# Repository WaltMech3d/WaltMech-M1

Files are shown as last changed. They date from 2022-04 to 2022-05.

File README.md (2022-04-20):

# `M1`

`The WaltMech M1 is the successor project of the MouseRig
- print volume: 150x150x150
- Framesize:    xyz 296x344x440 
- [Fusion 360 viewer](https://a360.co/3rA96aa)
- [Eva Parts](https://main.eva-3d.page/)



`summary of the changes and improvements:` 
- custom aluminum sheets have been removed
- the drive runs on ball bearings and 6mm belts
- the XY-drive was placed on top of the profiles
- the filter is integrated in the housing
- Reduced size of V2 compared to MouseRig 
- smaller motors were used for the Z axis
- blind joints instead of corner plates
- much less screws and hammer nuts
- The number of profiles has been reduced
- Easier to build and much more cost-efficient than the previous model



-----------------------------------------------------------------------
Special thanks to Liam Venter for letting me use his Ventermech Stars

[fastbikegear.co.nz](https://www.fastbikegear.co.nz/index.php?main_page=product_info&cPath=3717&products_id=12371)

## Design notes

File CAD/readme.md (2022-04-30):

30.04.2022:
Cad data have been updated. Radius on the filter box was adjusted + clearance for the cable of the fan was added.

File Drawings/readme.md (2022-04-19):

Drawings for:

- Side Panel with cutout
- Bottom Panel
- Back Panel Top
- Electro Panel
- Aluminium Plate for heated bed

The rest of the panels are rectangular with no cutouts. the dimensions can be taken from the CAD model or the BOM

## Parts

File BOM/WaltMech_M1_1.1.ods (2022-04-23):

1. ASM Frame + Enclosure
Pos. | Quantity | Designation | Dimension | Material / DIN | Supplier | Notes
1.01 | 4 | ALTRAX aluminum profile | 20x20x440 | Al | Hobby-store.pl (https://hobby-store.pl/profile-aluminiowe/typ-t-slot-20) | Special care should be applied when sourcing profiles. V-slot should be avoided, and bigger inside cores are encouraged to provide the strongest blind-joint connection. When using sliding t-nuts the groove should be of at least 6,5mm.
1.02 | 6 | ALTRAX aluminum profile | 20x20x304 | Al
1.03 | 7 | ALTRAX aluminum profile | 20x20x256 | Al
1.04 | 2 | ALTRAX aluminum profile | 20x20x225 | Al
1.05 | 1 | ALTRAX aluminum profile | 20x20x205 | Al
1.06 | 1 | ALTRAX aluminum profile | 20x20x267 | Al
1.07 | 64 | T Nut | m4 | TypB | Aliexpress (https://de.aliexpress.com/item/33024399415.html?pdp_ext_f=%7b%22sku_id%22%3A%2267203262268%22%7d)
1.08 | 102 | T Nut | m3 | Typ B | Aliexpress (https://de.aliexpress.com/item/33024399415.html?pdp_ext_f=%7b%22sku_id%22%3A%2267203262268%22%7d)
1.09 | 9 | Nut | m4 | DIN 934
1.10 | 28 | Nut | m3 | DIN 934
1.11 | 4 | Ny-lock Nut | m5 | DIN 982
1.12 | 16 | Threaded Insert m3 | m3x5x4 |  | Aliexpress (https://de.aliexpress.com/item/4000232858343.html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)
1.13 | 24 | Washer | m5 | DIN 125
1.14 | 4 | m3x5 cylindrical | m3 | DIN 912
1.15 | 4 | m3x6 cylindrical | m3 | DIN 912
1.16 | 4 | m3x6 Countersunk | m3 | DIN 7991
1.17 | 125 | m3x8 cylindrical | m3 | DIN 912
1.18 | 8 | m3x10 Countersunk | m3 | DIN 7991
1.19 | 6 | m3x14 Countersunk | m3 | DIN 7991
1.20 | 35 | m3x14 cylindrical | m3 | DIN 912
1.21 | 44 | m4x10 Button-Head Screw | m4 | ISO 7380-1
1.22 | 12 | m4x12 Button-Head Screw | m4 | ISO 7380-1
1.23 | 13 | m4x20 Button-Head Screw | m4 | ISO 7380-1
1.24 | 4 | m4x35 Button-Head Screw | m4 | ISO 7380-1
1.25 | 37 | m5x16 Button-Head Screw | m5 | ISO 7380-1
1.26 | 3 | m5x16 Countersunk | m5 | DIN 7991
1.27 | 2 | m5x20 cylindrical | m5 | DIN 912
1.28 | 4 | m5x35 Button-Head Screw | m5 | ISO 7380-1
1.29 | 4 | m5x45 Button-Head Screw | m5 | ISO 7380-1
1.30 | 8 | ST FAN-SCREW | 5x10 |  |  | supplied with fans
1.31 | 1 | Front Panel | 440x296x3 | acrylic glass
1.32 | 2 | Side Panel | 414x318x3 | ABS
1.33 | 1 | Top Panel | 318x270x3 | ABS
1.34 | 1 | Lower back Panel | 280x270x3 | ABS
1.35 | 1 | Top back Panel | 270x147x3 | ABS
1.36 | 1 | Bottom Panel | 256x234x3 | ABS
1.37 | 2 | Skirt Panel 1 | 304x30x3 | ABS
1.38 | 2 | Skirt Panel 2 | 256x30x3 | ABS
1.39 | 1 | Elektro Panel | 440x296x3 | ABS
2. Linear guide , Bed , etc.
Pos. | Quantity | Designation | Dimension | Material / DIN | Supplier | Notes
2.01 | 1 | MGN12C | 200mm |  | Aliexpress (https://de.aliexpress.com/item/32829826159.html?scm_id=1007.22922.122102.0&scm-url=1007.22922.122102.0)
2.02 | 5 | MGN9H | 200mm |  | Aliexpress (https://de.aliexpress.com/item/32773296501.html?spm=a2g0o.cart.0.0.697a3c00QbYMLn&mp=1)
2.03 | 3 | Spider Coupler | Ø20x25 /5-8 |  | Aliexpress (https://fr.aliexpress.com/item/32576954099.html?pdp_ext_f=%7b%22sku_id%22%3A%2264792222206%22%7d)
2.04 | 3 | Lead Screw | TR8x4x210 |  | Aliexpress (https://de.aliexpress.com/item/1005003425426272.html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)
2.05 | 2 | Nema17 x 48 | 42x42x48 |  | Stepperonline (https://www.omc-stepperonline.com/de/nema-17-42mm-schrittmotor/nema-17-bipolar-59ncm-84oz-in-2a-42x48mm-4draehte-w-1m-kabel-verbinder-17hs19-2004s1)
2.06 | 3 | Nema17 x 40 | 42x42x40 |  | Stepperonline (https://www.omc-stepperonline.com/de/nema-17-42mm-schrittmotor/nema-17-bipolar-45ncm-64oz-in-2a-42x42x40mm-4-draehte-w-1m-kabel-verbinder-17hs16-2004s1)
2.07 | 6 | Thrust Bearing F8-16M |  | 8x16x5mm | Aliexpress (https://de.aliexpress.com/item/32912814515.html?spm=a2g0o.cart.0.0.adcf3c000MXIuY&mp=1)
2.08 | 2 | End-stops |  |  | Aliexpress (https://de.aliexpress.com/item/32817694814.html?pdp_ext_f=%7b%22sku_id%22%3A%2264691411626%22%7d)
2.09 | 2 | Timing Pulley GT2 |  | 20T | Aliexpress (https://de.aliexpress.com/item/32788162034.html)
2.10 | 1 | PTFE Tube | 2x4 |  | Aliexpress (https://de.aliexpress.com/item/1005001408141263.html)
2.11 | 1 | GT2 Belt | 6mm x3m |  | Aliexpress (https://de.aliexpress.com/item/32853559638.html)
2.12 | 24 | Ball-bearing F695-2RS | 5 x 13 x 4 | FUSHIBEARING | Amazon, Aliexpress
2.13 | 4 | Neodymium magnet | Ø6x4 |  | Aliexpress (https://fr.aliexpress.com/item/4001165760765.html)
2.14 | 3 | Neodymium magnet 2 Holes | 20x10x4 |  | Aliexpress, RatRig
2.15 | 1 | Drag Chain 1m | 10x11 |  | aliexpress (https://www.aliexpress.com/item/33000014666.html)
2.16 | 4 | Rubber Feet | 20x15x8 |  | aliexpress (https://www.aliexpress.com/item/32980790365.html?scm_id=1007.40000.267768.0&scm-url=1007.40000.267768.0)
2.17 | 1 | Silicon heat pad | 120x120 |  | Keenovo (https://keenovo.store/collections/standard-keenovo-silicone-heaters/products/keenovo-square-silicone-heater-3d-printer-build-plate-heatbed-heating-pad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)
2.18 | 1 | PEI | 150x150 |  | Aliexpress (https://de.aliexpress.com/item/1005003636696916.html)
2.19 | 3 | Spacer | m5x6 |  | Aliexpress (https://de.aliexpress.com/item/33021606483.html?spm=a2g0o.cart.0.0.4d153c00YnOYJ2&mp=1)
2.20 | 3 | Threaded round ball | Ø12-m5 |  | Aliexpress (https://de.aliexpress.com/item/33014236308.html)
2.21 | 1 | Aluminum Plate | 165x165x6 |  | Clever3d | Easy to self source, but Clever3d offers an attractive price point for a milled cast aluminum plate for european based builders.
2.22 | 6 | Stainless dowel | Ø3x28mm |  | Amazon (https://www.amazon.de/gp/product/B00OK6GJNM/ref=ppx_yo_dt_b_asin_image_o04_s00?ie=UTF8&psc=1)
3. Print head example
Pos. | Quantity | Designation | Dimension | Material / DIN | Supplier | Notes
3.01 | 1 | Phaetus Dragon Standard Flow
3.02 | 1 | LDO Orbiter 2
3.03 | 1 | thermistor
3.04 | 1 | cartridge heater
3.05 | 1 | Blower fan | 50x15
3.06 | 1 | Axial fan | 40x40x15
3.07 | 1 | Sensor LJ12A3-4-Z/BX | m12 |  | Amazon (https://www.amazon.de/gp/product/B07XGFTV2F/ref=ppx_yo_dt_b_asin_image_o06_s00?ie=UTF8&psc=1)
4. Electronics
Pos. | Quantity | Designation | Dimension | Material / DIN | Supplier | Notes
4.01 | 1 | BTT Octopus |  |  | Amazon (https://www.amazon.de/BIGTREETECH-Mainboard-Controlle-Unterstützt-Unterstützung/dp/B098QHVBXC)
4.02 | 1 | Mean Well UHP-350-24 |  |  | Conrad (https://www.conrad.de/de/p/mean-well-uhp-350-24-ac-dc-einbaunetzteil-14-6-a-350-4-w-25-2-v-dc-ausgangsspannung-regelbar-1838048.html) | for 24v heat-bed
4.03 | 1 | Mean Well UHP-200-24 |  |  | Conrad (https://www.conrad.de/de/p/mean-well-uhp-200-24-ac-dc-einbaunetzteil-8-4-a-25-2-v-dc-ausgangsspannung-regelbar-1838286.html) | for 230v heat-bed ->recommended
4.04 | 1 | Raspberry pi Zero 2 W |  |  | BerryBase (https://www.berrybase.de/raspberry-pi/raspberry-pi-computer/boards/raspberry-pi-zero-2-w)
4.05 | 1 | SSR-25DA Fotek |  |  | Hobby-store.pl (https://hobby-store.pl/en/relays/ssr-25da-fotek-solid-state-relay-25a.html)
4.06 | 2 | be Quiet! Fan | 80mm |  | Amazon (https://www.amazon.de/quiet-BL044-Pure-Wings-Gehäuselüfter/dp/B00IOIJ4AC?__mk_de_DE=ÅMÅŽÕÑ)
4.07 | 1 | OBO Bettermann A8 | 75x75 |  | Amazon
4.08 | 6 | TMC 2209 Stepper |  |  | Aliexpress (https://de.aliexpress.com/item/33029587820.html)
4.09 | 1 | COB LED | 24v 5mm x 1m |  | Aliexpress (https://de.aliexpress.com/item/1005002701379459.html)
4.10 | 1 | Power switch |  |  | Amazon (https://www.amazon.de/gp/product/B01H5MK3OI/ref=ppx_yo_dt_b_asin_image_o05_s00?ie=UTF8&psc=1)

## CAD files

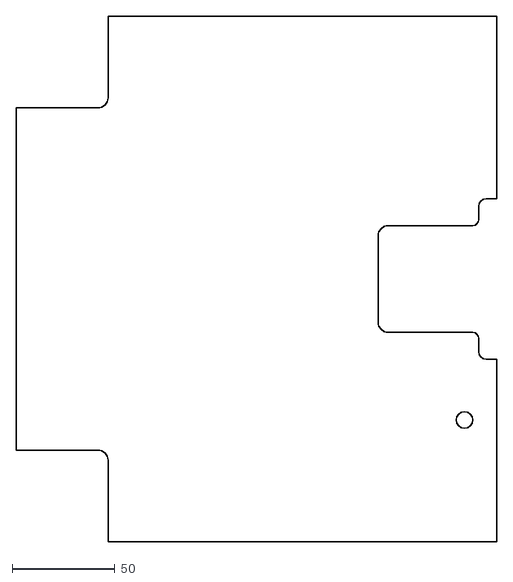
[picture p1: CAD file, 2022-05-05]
Drawings/Bottom_Panel.dxf
233.5 x 255.5

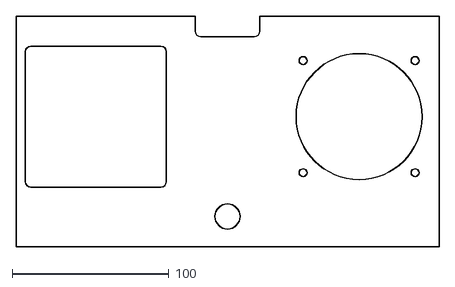
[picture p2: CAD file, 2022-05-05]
Drawings/Top_Back_Panel.dxf
270.0 x 147.0

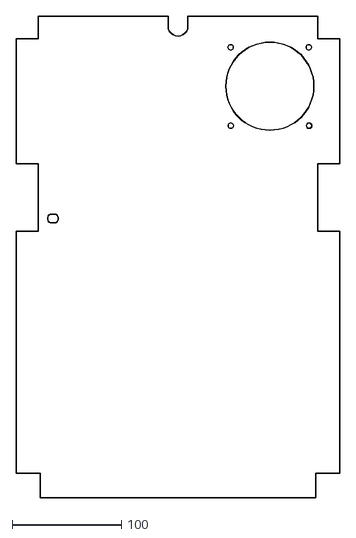
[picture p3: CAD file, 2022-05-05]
Drawings/Electronics_Panel.dxf
296.0 x 439.6

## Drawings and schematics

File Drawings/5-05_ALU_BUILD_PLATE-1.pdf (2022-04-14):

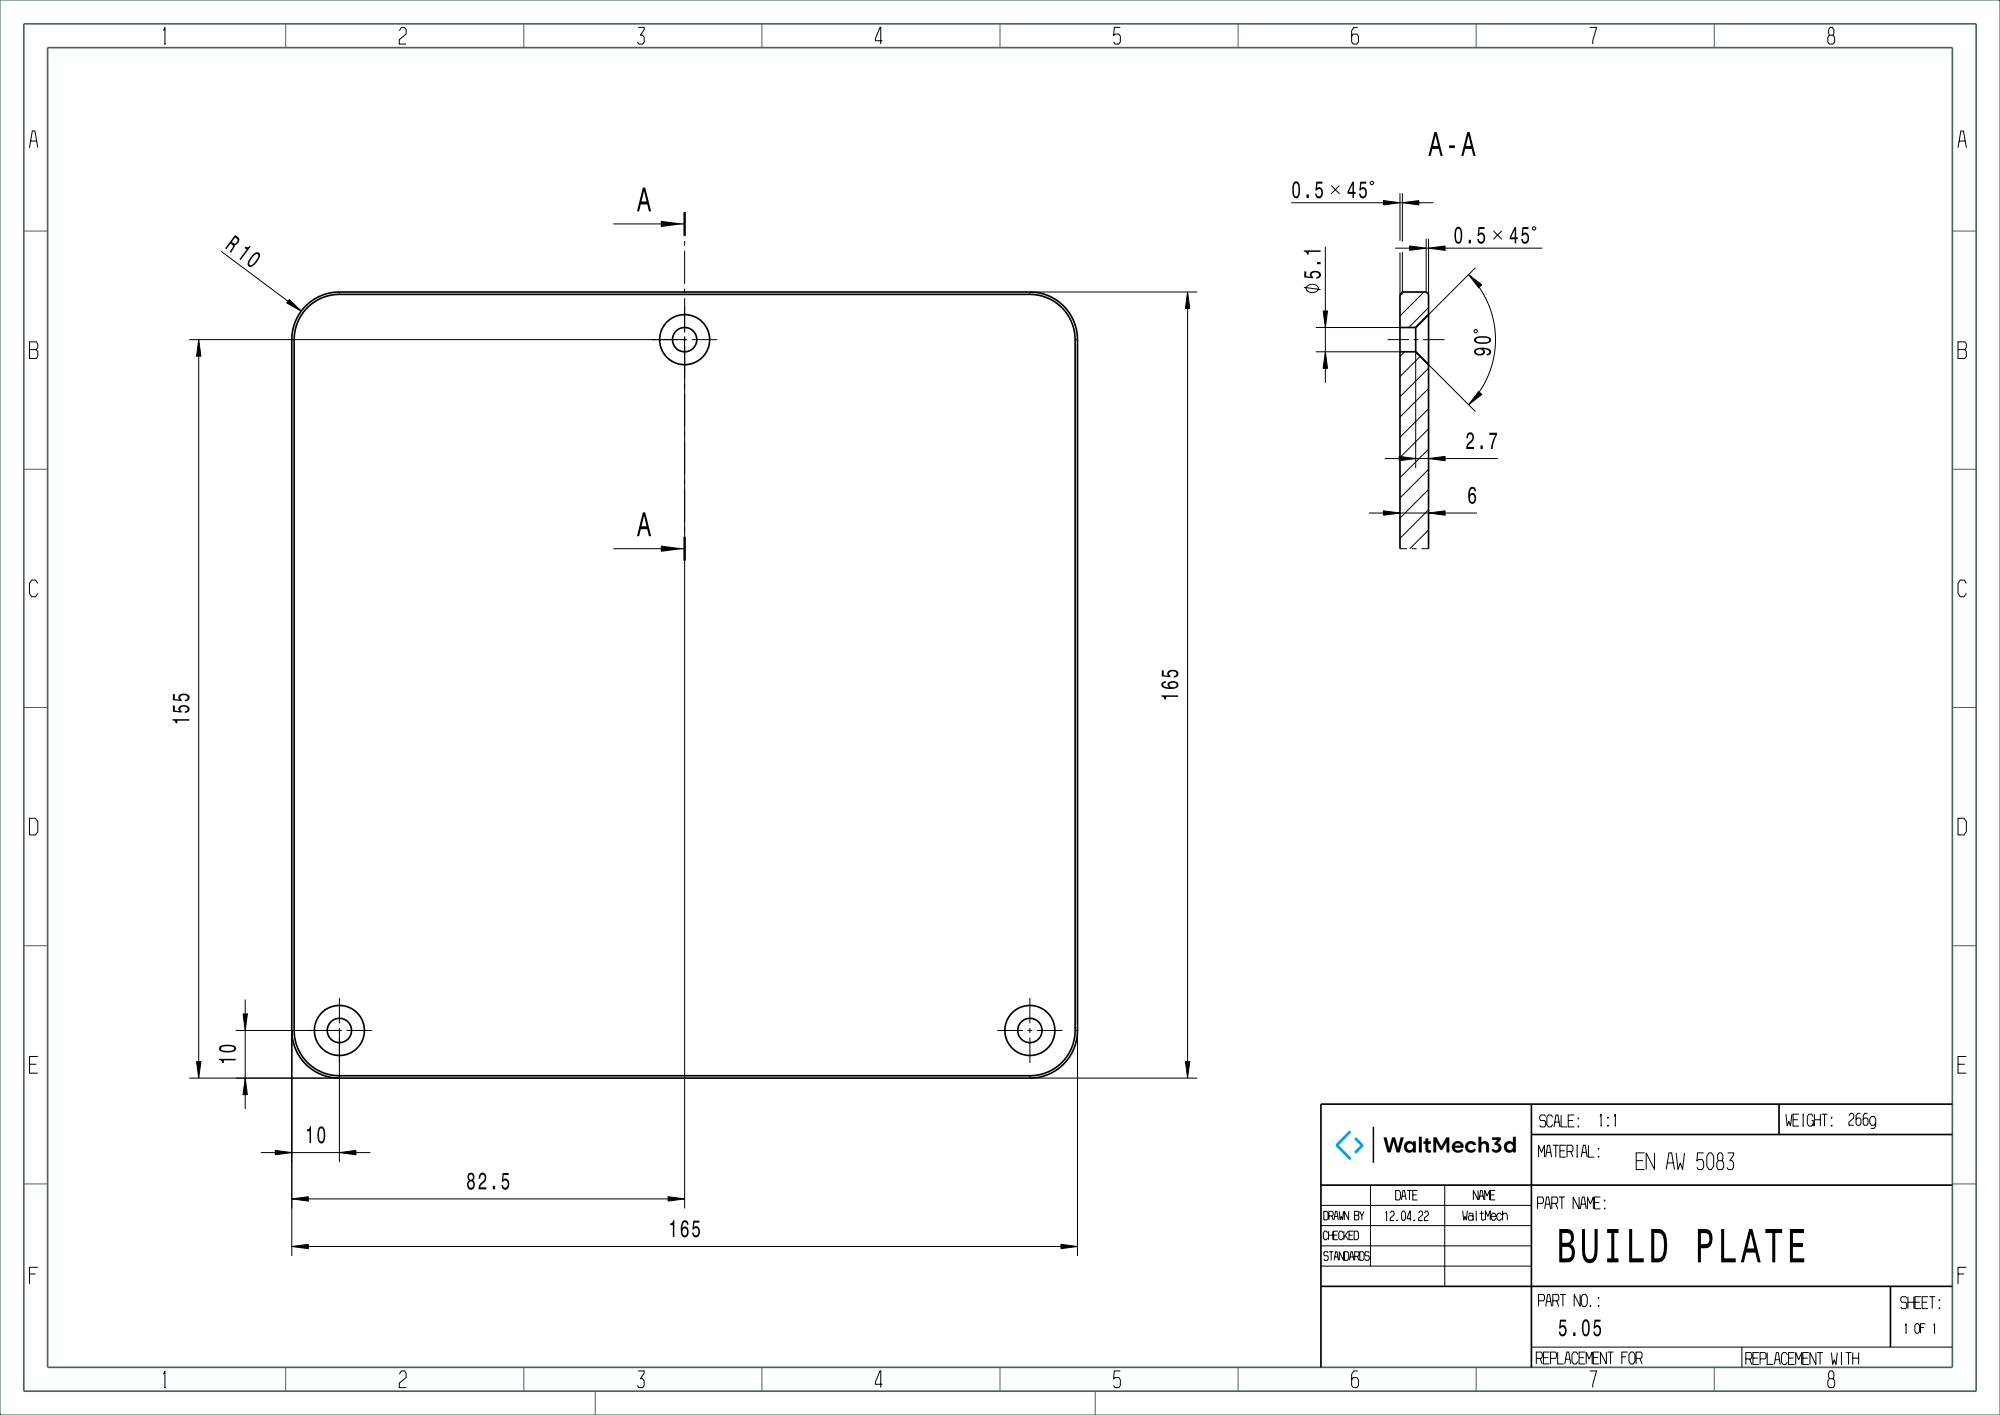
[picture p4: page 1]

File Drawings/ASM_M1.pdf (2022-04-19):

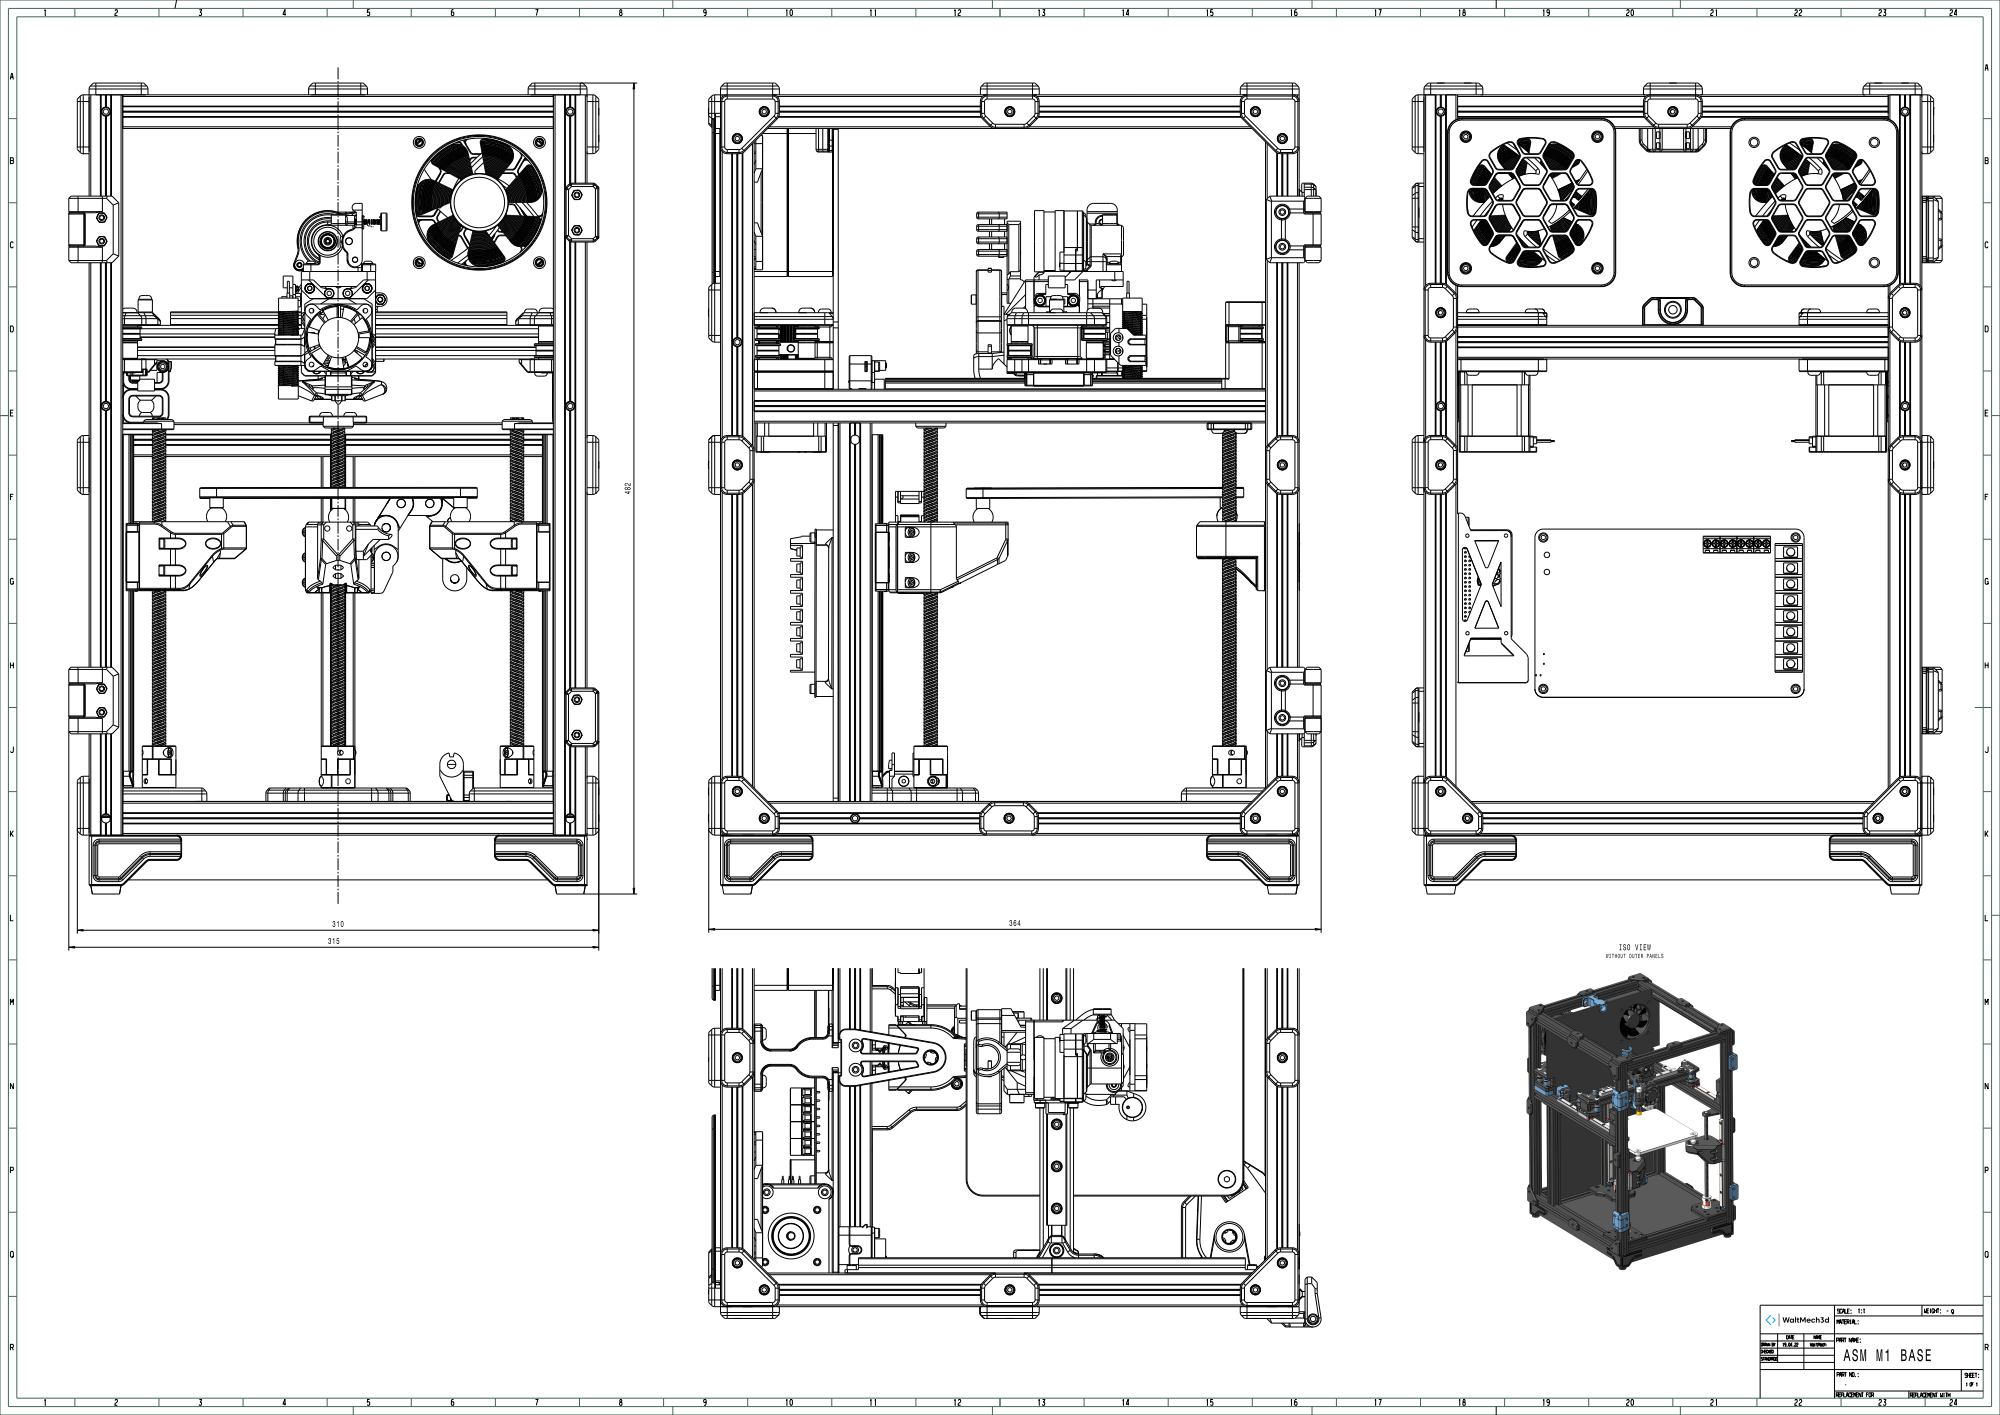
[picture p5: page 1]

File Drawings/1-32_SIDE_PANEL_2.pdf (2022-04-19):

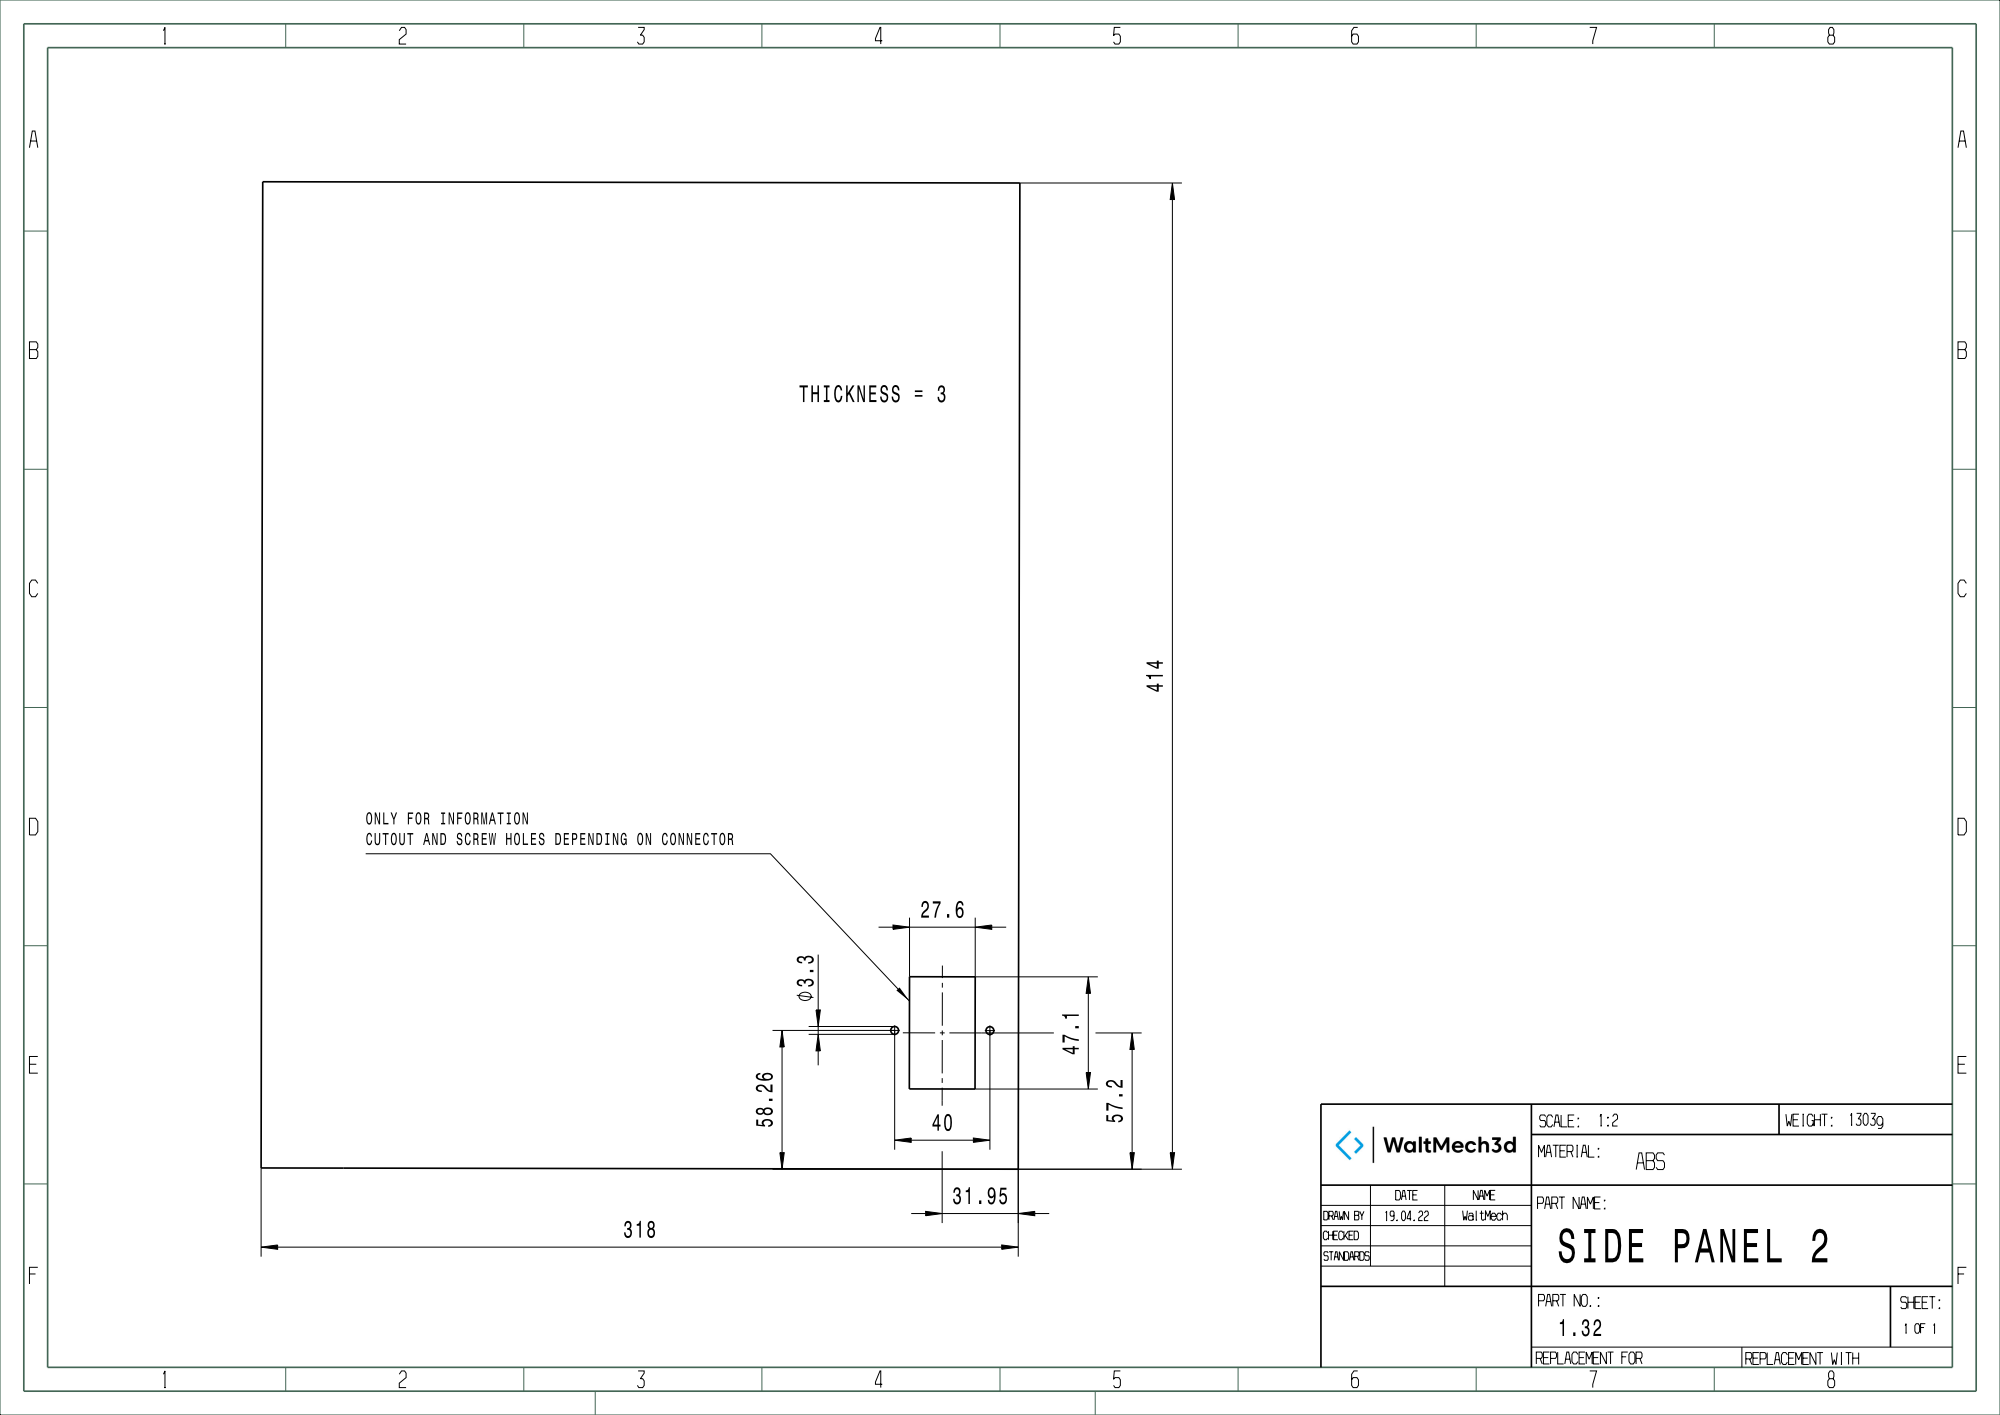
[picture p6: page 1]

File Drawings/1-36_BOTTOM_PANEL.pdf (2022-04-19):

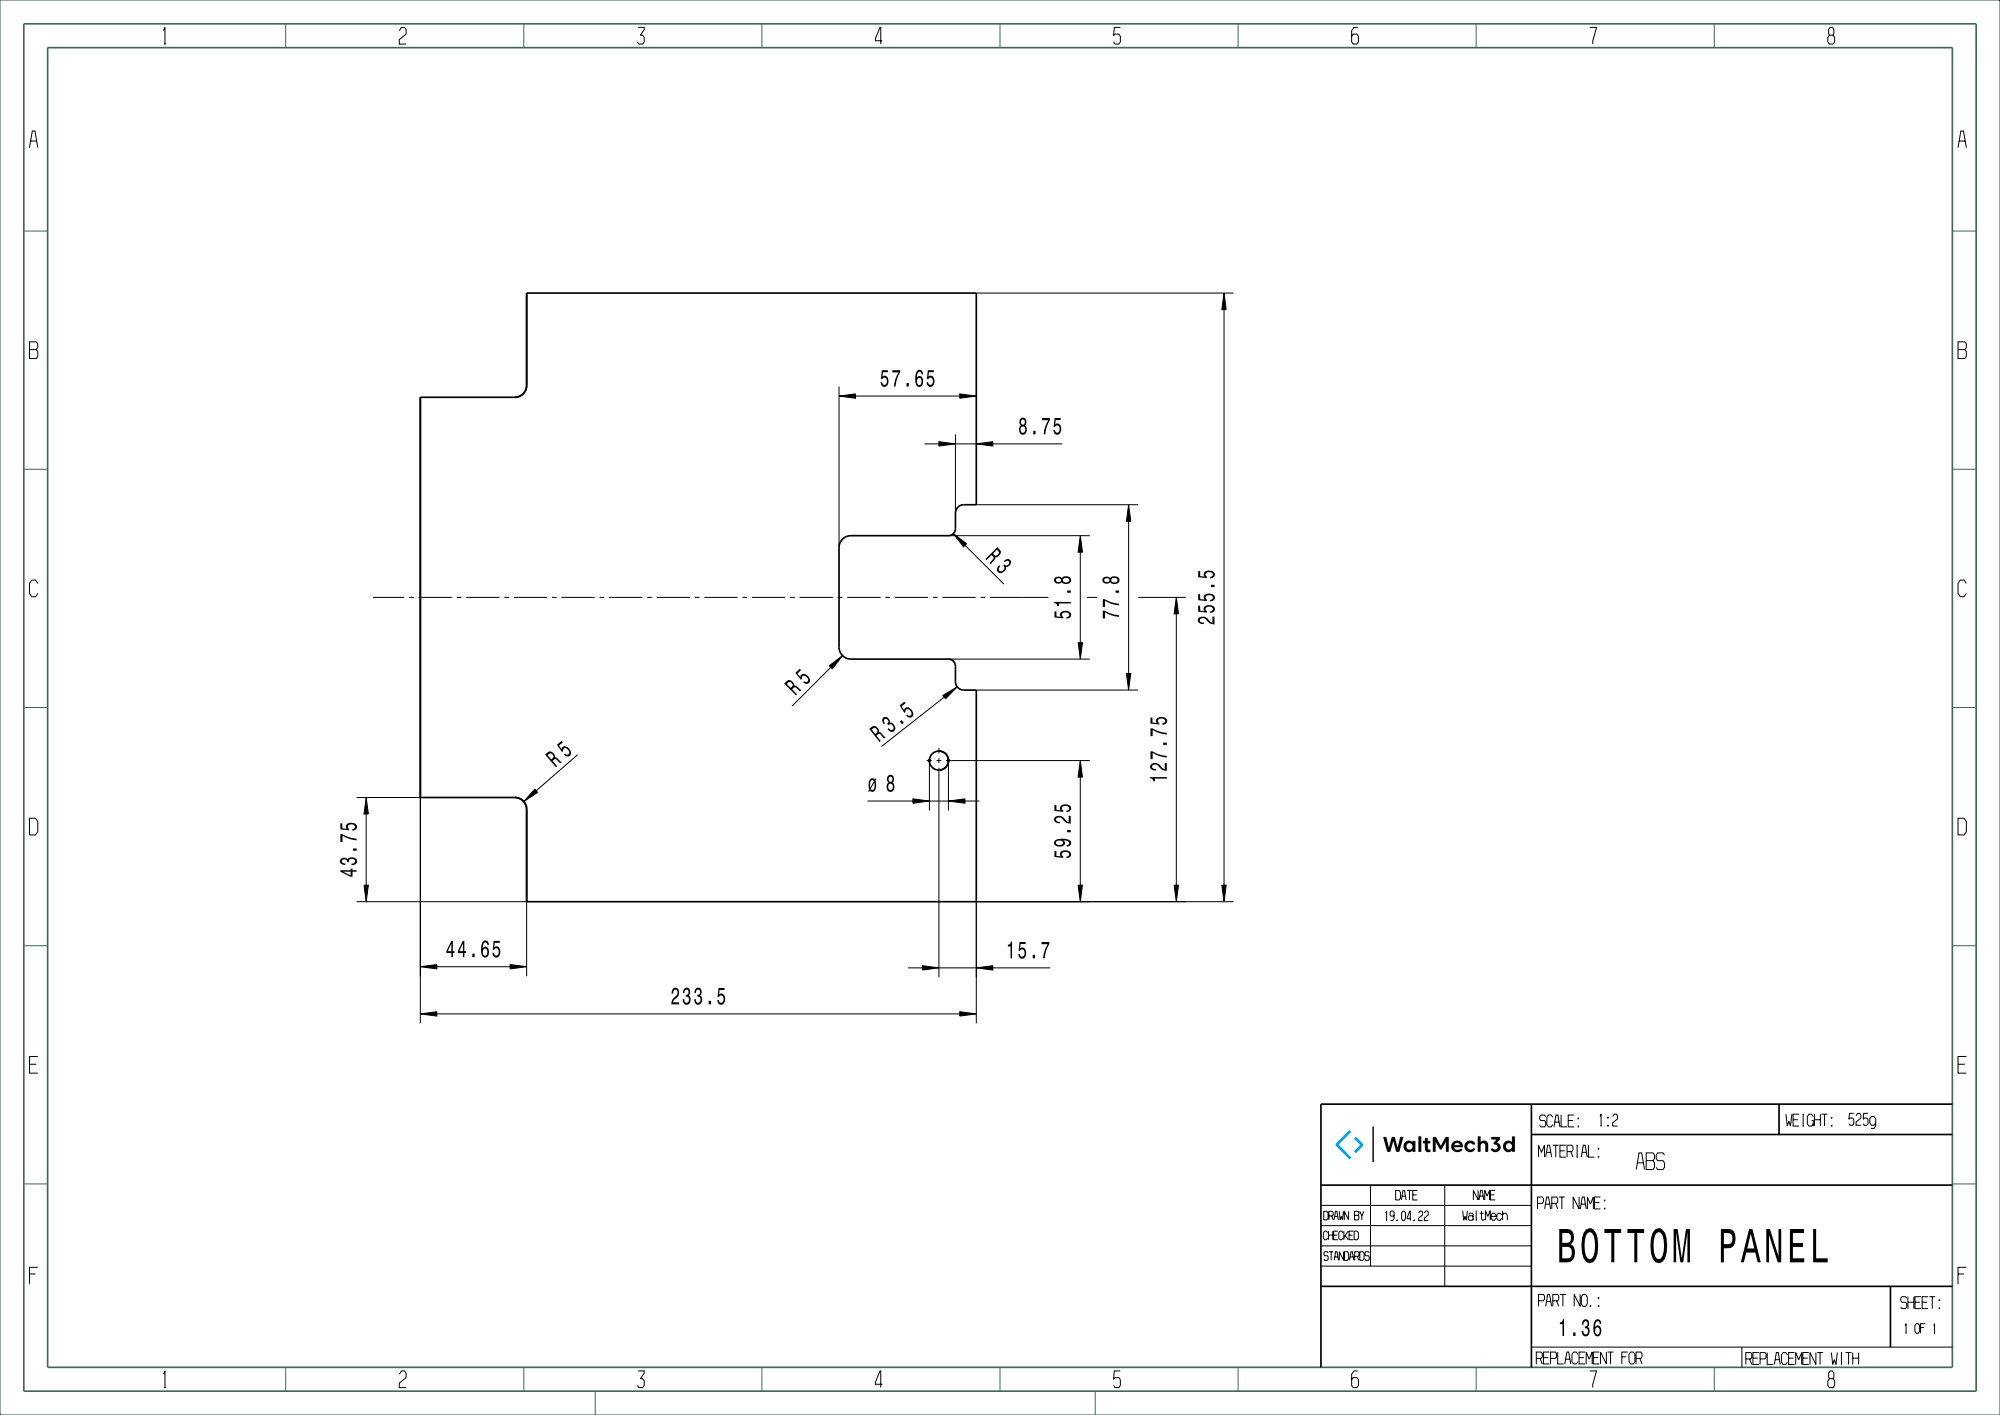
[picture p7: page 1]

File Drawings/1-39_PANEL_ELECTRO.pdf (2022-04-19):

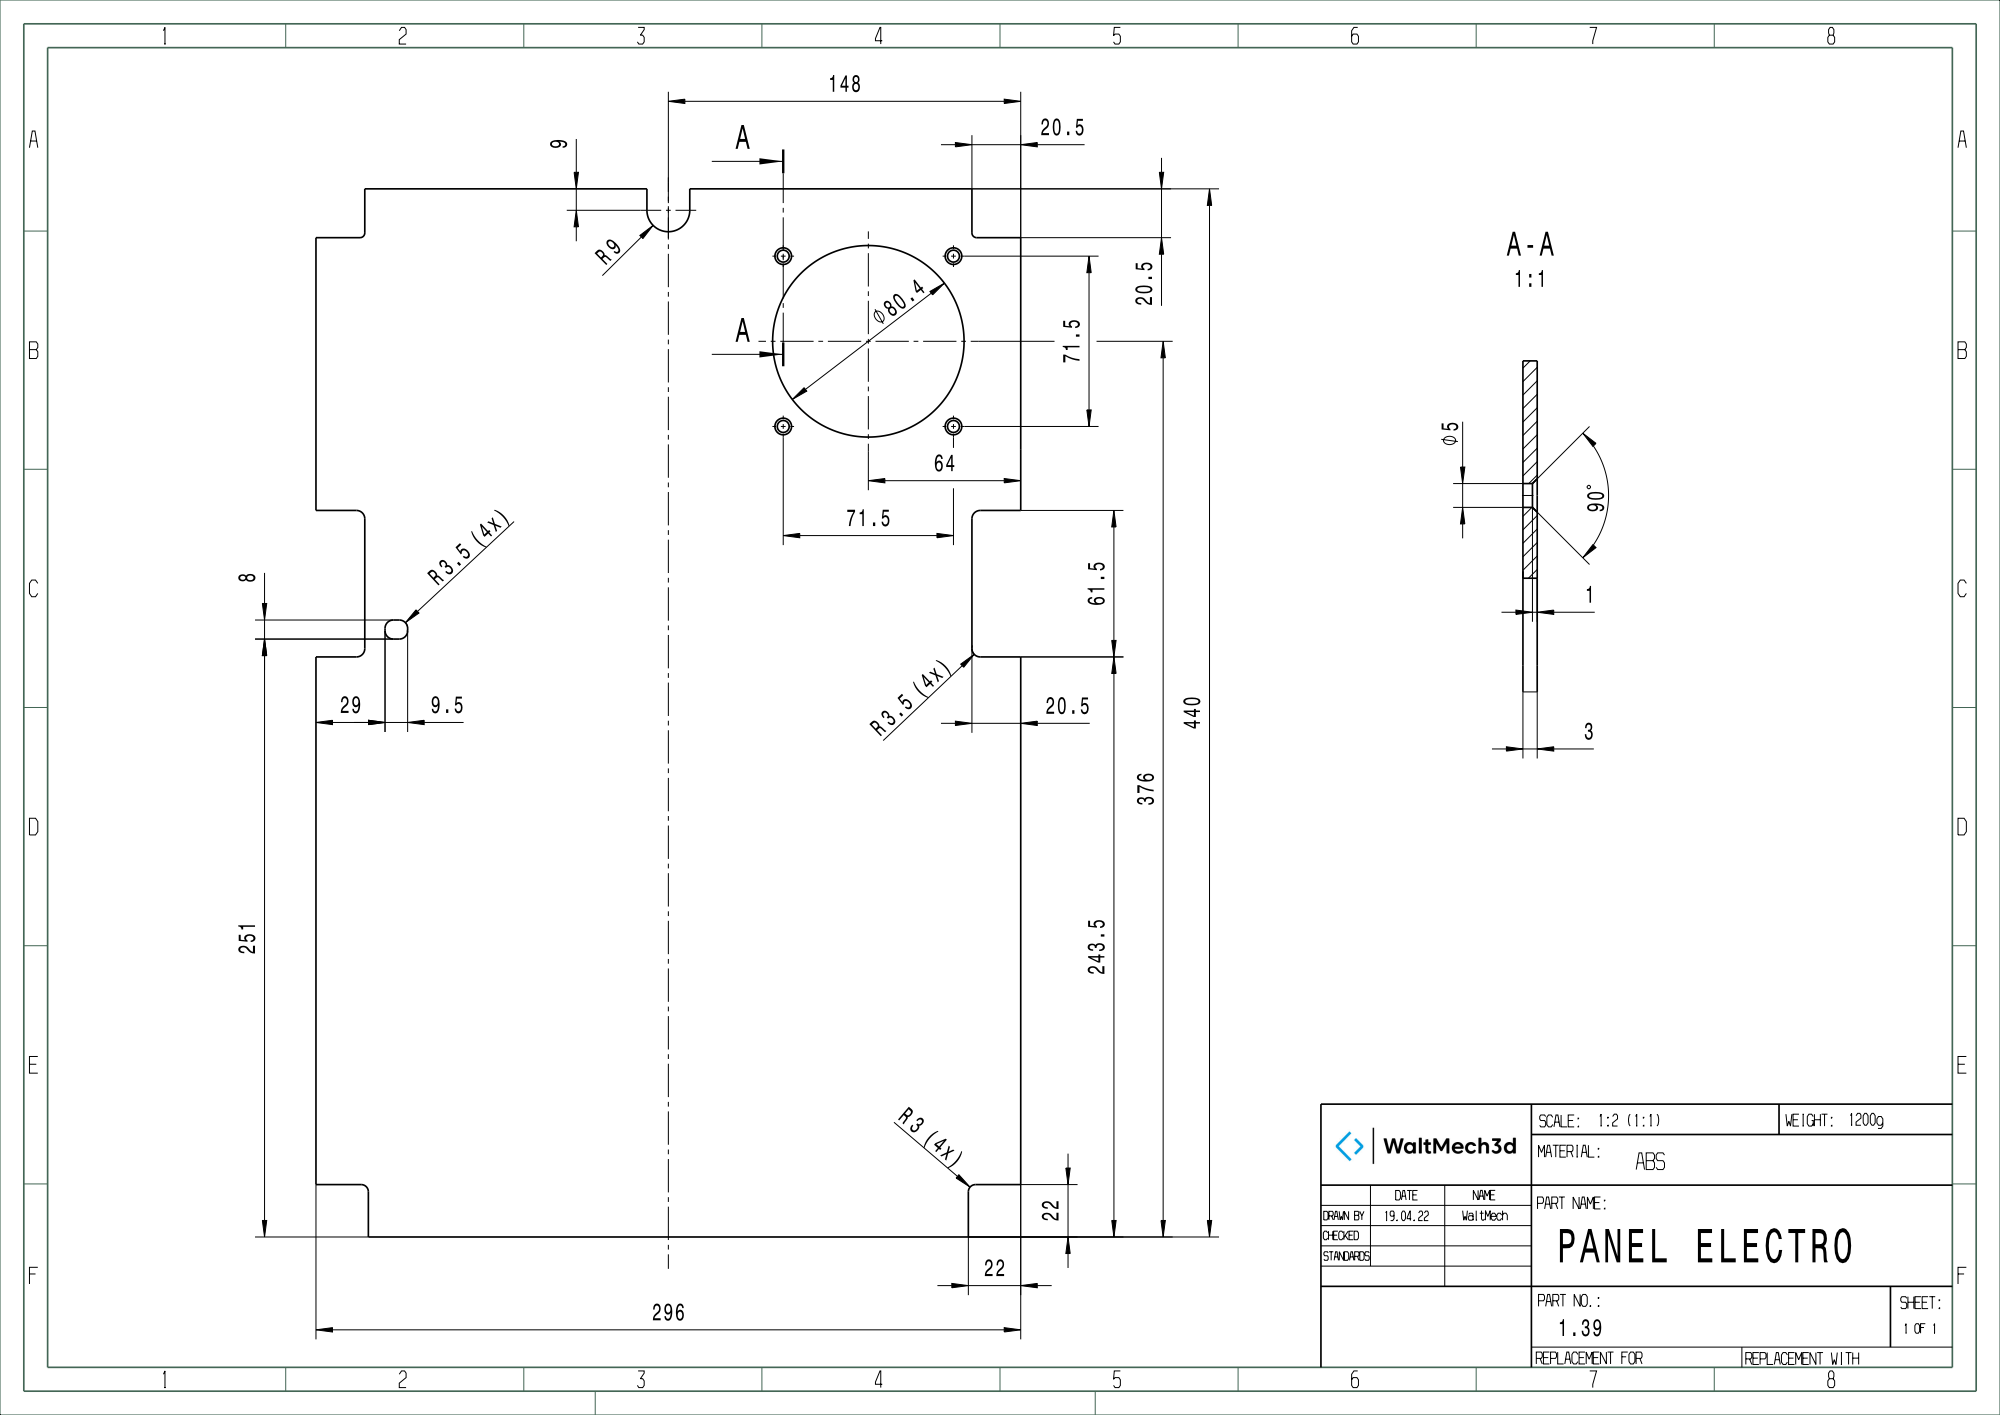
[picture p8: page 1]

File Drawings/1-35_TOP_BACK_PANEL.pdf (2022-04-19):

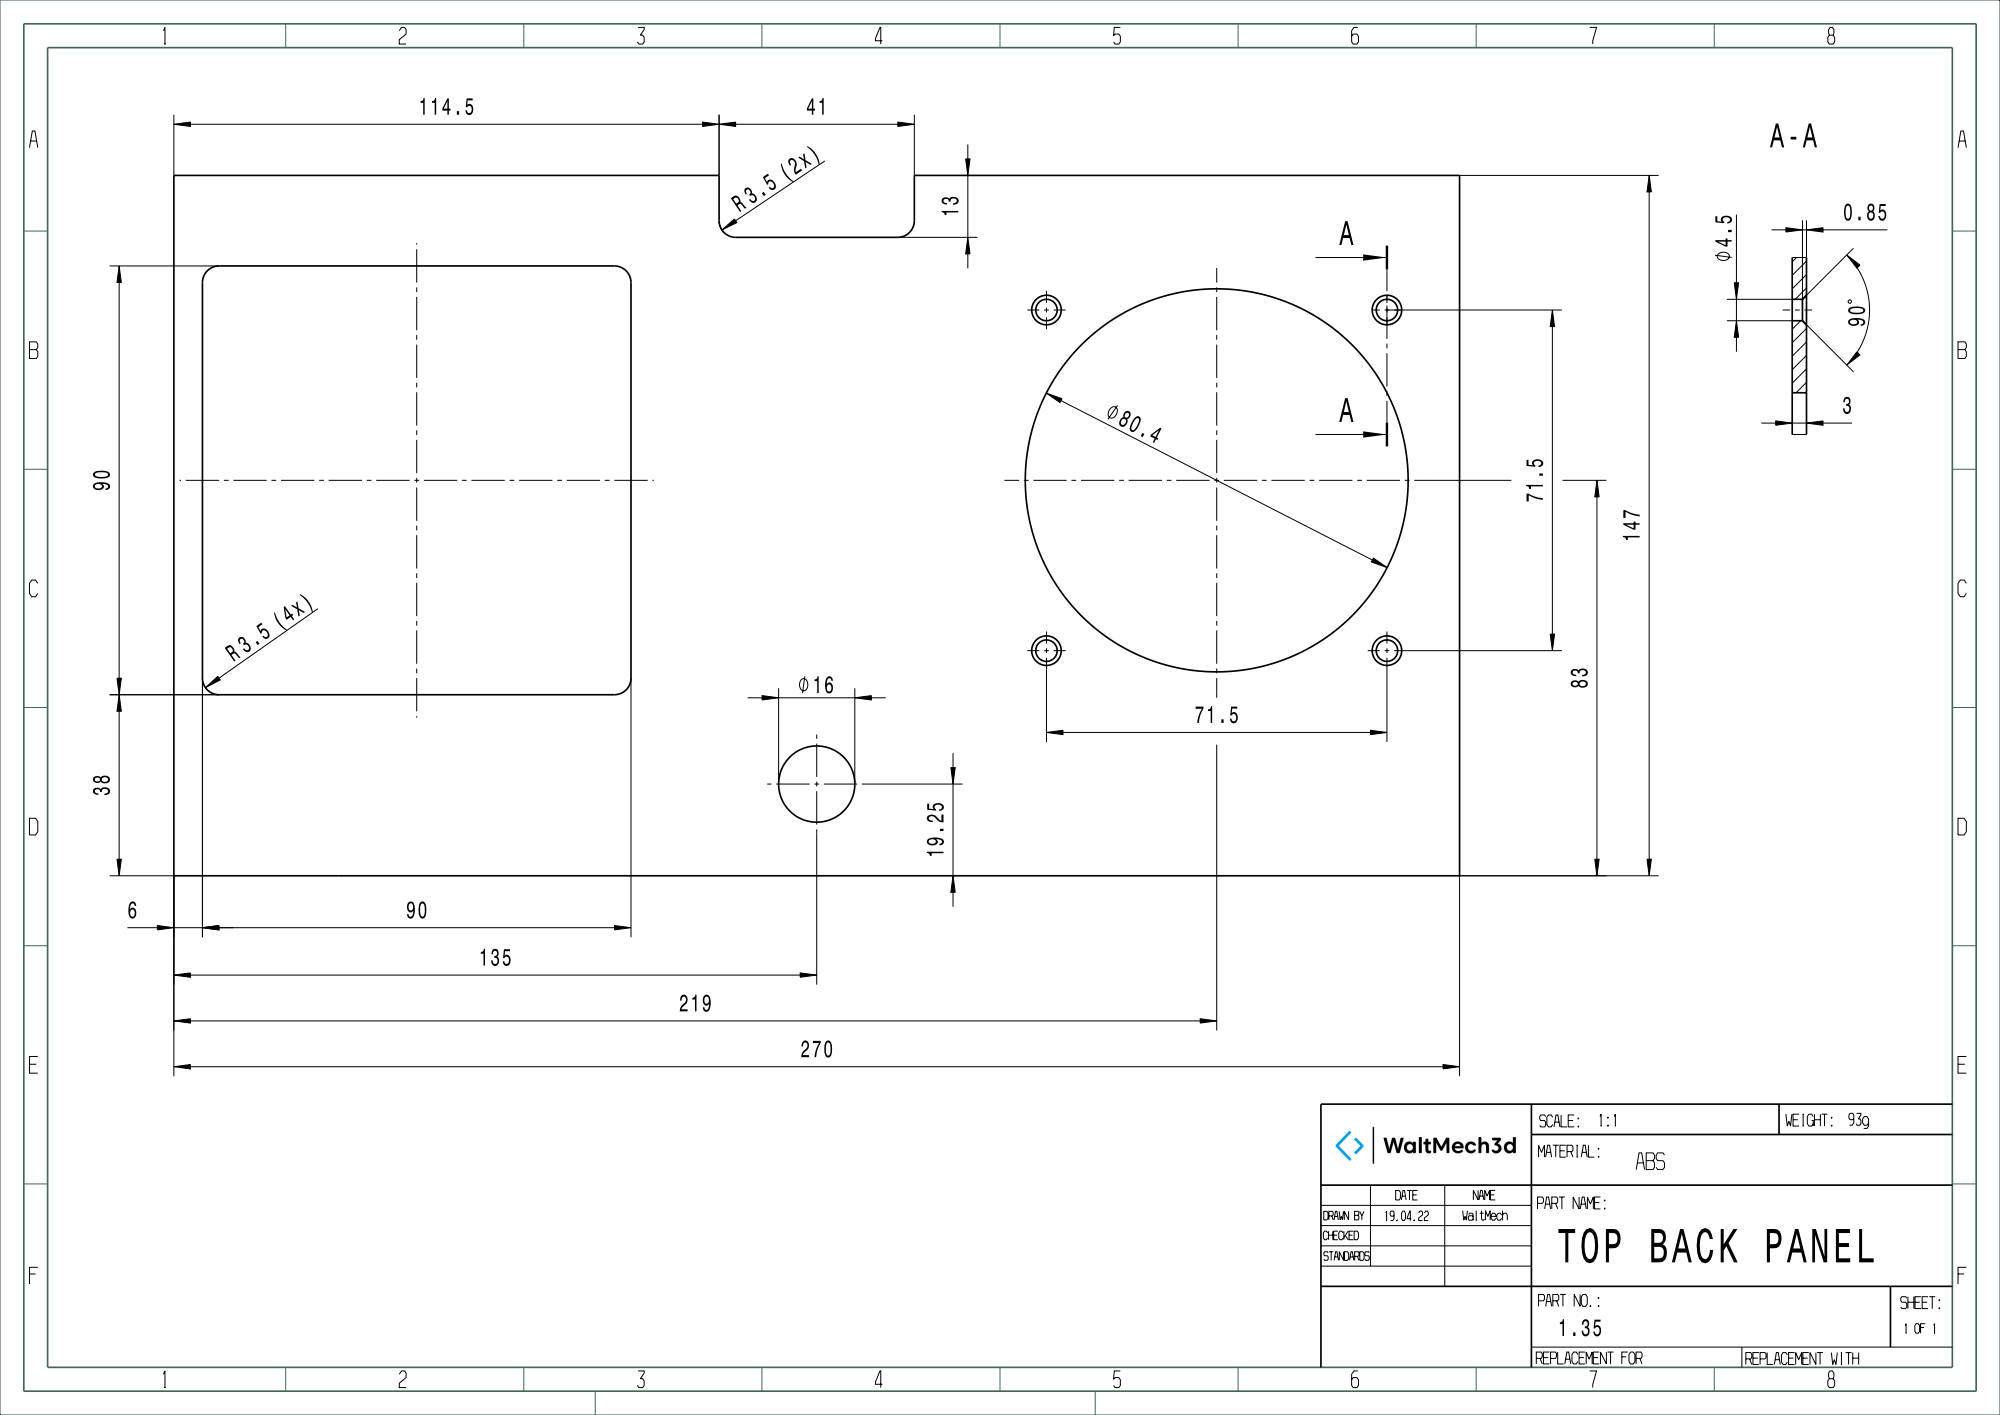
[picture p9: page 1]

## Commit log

2022-04-14 New BOM structure.
    [BOM_V2_1.0.ods]
2022-04-14 Check links
    [BOM_V2_1.0.ods]
2022-04-19 BOM WIP
    [BOM_V2_1.0.ods]
2022-04-19 BOM update
    [BOM_V2_1.0.ods]
2022-04-19 BOM fix
    [BOM_V2_1.1.ods]
2022-04-19 BOM namefix
    [BOM_V2_1.1.ods]
2022-04-23 BOM link update
    [WaltMech_M1_1.1.ods]
2022-04-30 Create CAD
2022-05-05 Electronics Panel DXF upload
    [Electronics_Panel.dxf]
2022-05-05 Bottom and Back top panel DXF upload
    [Bottom_Panel.dxf, Top_Back_Panel.dxf]
